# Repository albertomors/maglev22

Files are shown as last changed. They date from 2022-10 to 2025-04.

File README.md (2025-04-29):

# Re-design of a magnetic levitation platform: from an early prototype to a working system
Bachelor Thesis in Electronic Engineering - November 2022 - Università degli Studi di Padova @unipd

## Abstract
This work documents the modelling and re-designing of a maglev platform intended to become a take-home lab for students interested in control engineering. The platform, initially designed by a team of Norwegian students, presented a series of inefficiencies and limitations that this work seeks to remove. Thus, the final goal of this project is to fully develop and test an improved maglev platform.

The thesis introduces both the theoretical framework behind the modeling of the system, and the specific frameworks for designing and analysing the various electronic subsystems that were deemed to be improvable. In doing so, this work discusses those subsystems, lists a set of potential solutions together with their pros and cons, and selects potential choices one may take, given the techno-economic constraints surrounding the project. In addition, practical implementation issues are discussed, giving in this way an overview of which parts of the systems should be further analyzed and fine tuned before arriving at a system that is ready for production. 

The most challenging part of this project has been entering into it without clear guidelines of the design choices made by the previous team. It is precisely for this reason that this work does not just aim at reporting on the project itself, but also at offering documentation that is as clear as possible, intended to help a potential future team bringing the project to its next phase.

[Click here to read the dissertation](https://github.com/albertomors/maglev22/blob/b5a09330e3dea7a6b91397591241a9633b680332/Bachelor%20Thesis%20-%20maglev22.pdf)

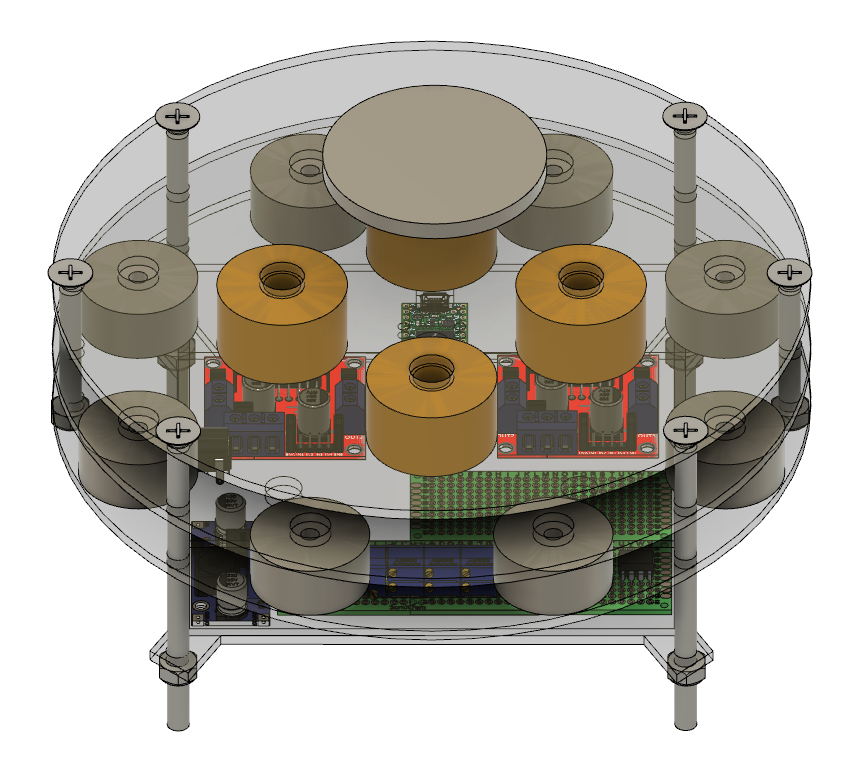
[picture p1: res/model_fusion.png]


## Structure

```
maglev22/
├── code                               # C++/arduino code for the Teensy4.0 microcontroller
├── datasheets                         # details about the electronic components used in the project  
├── matlab                             # modelling scripts   
├── schematics                         # kicad, fritzing and multisim schematics
├── Bachelor Thesis - maglev22.pdf     # Dissertation
├── LICENSE                            # License information
├── README.md                          # Project documentation
└── model_fusion.png                   # Picture of the prototype built
```

## What's next
In the meantime the project has moved on, see https://github.com/Hansolini/Take-home-Maglev-lab for the main repo handling this project. I contributed again to it with the design of the PCB for it's version 2.6 and 3.0. Below some videos and pictures of them.

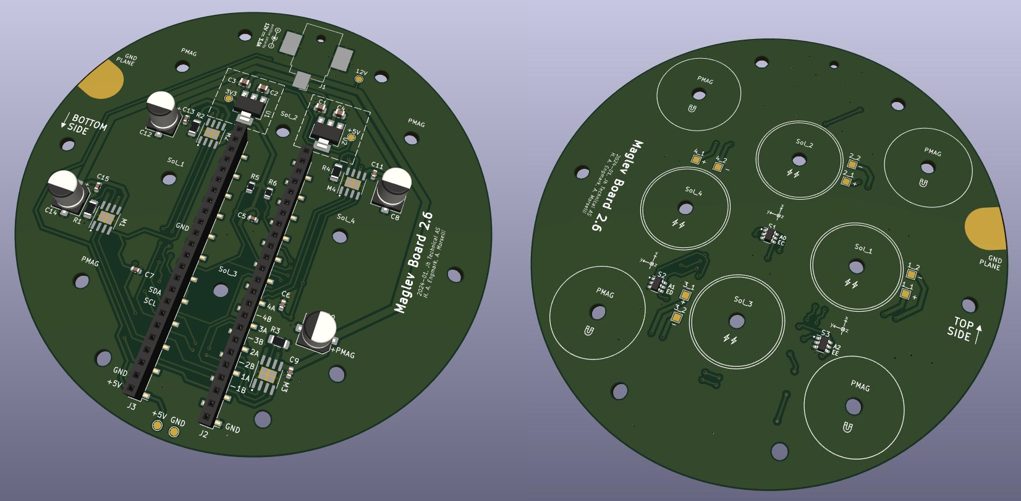
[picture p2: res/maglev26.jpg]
 \
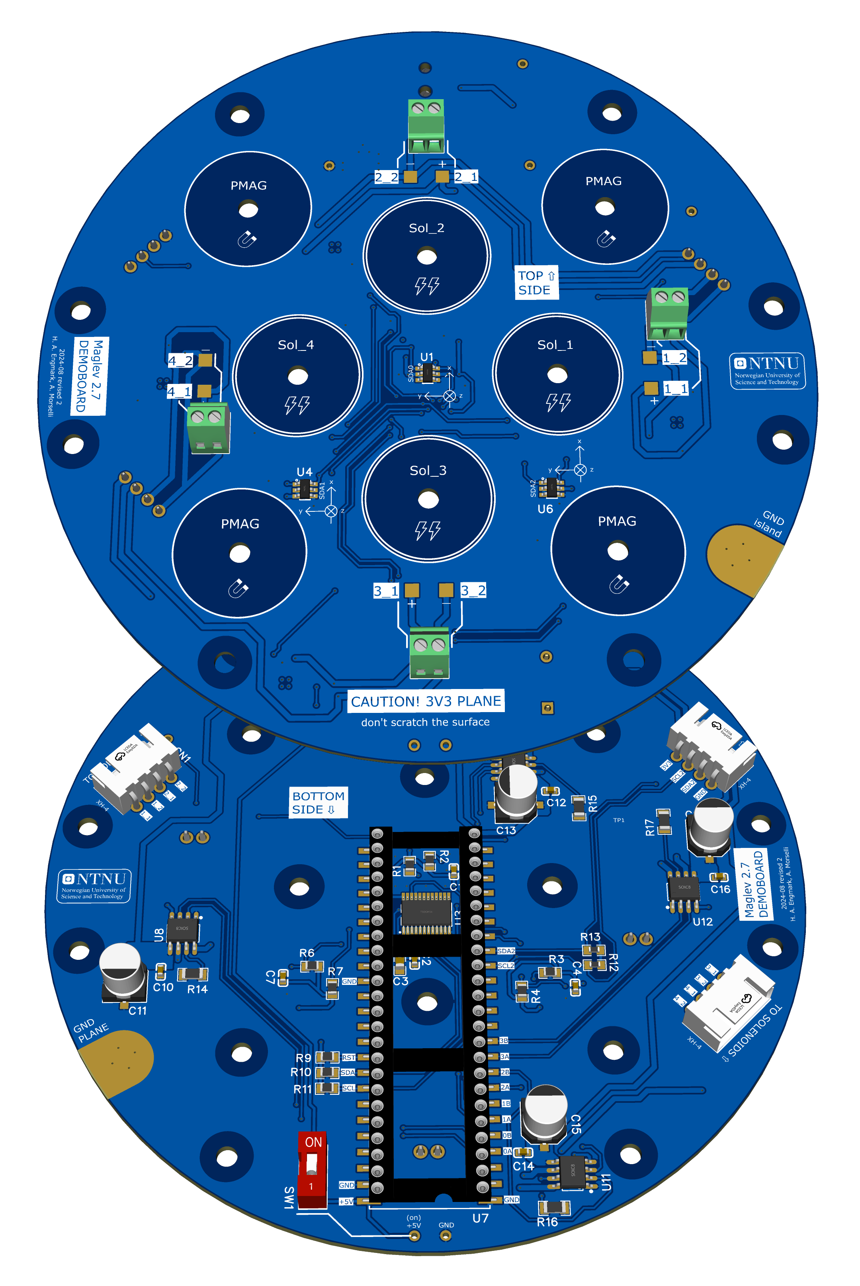
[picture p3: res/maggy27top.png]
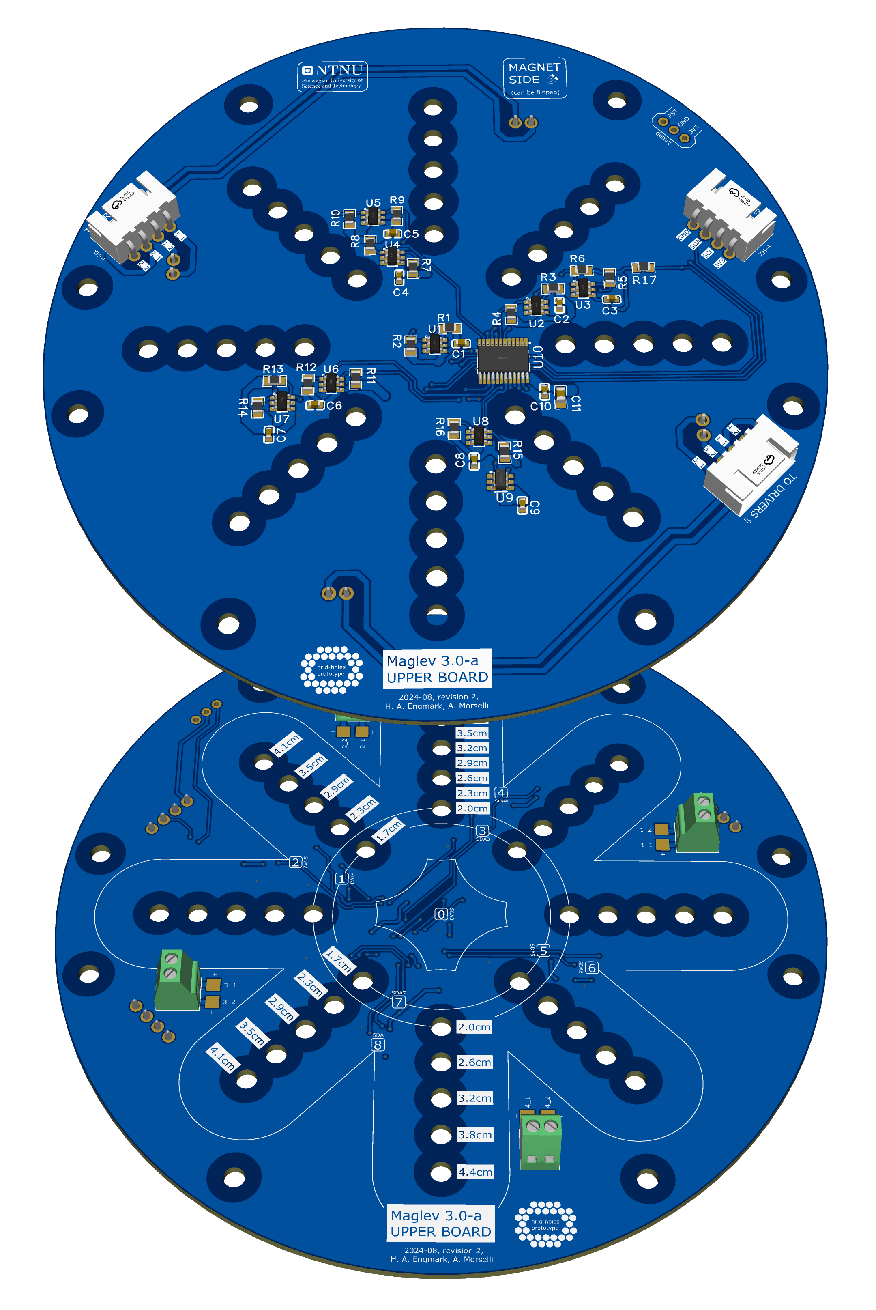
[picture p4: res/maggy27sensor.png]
  \
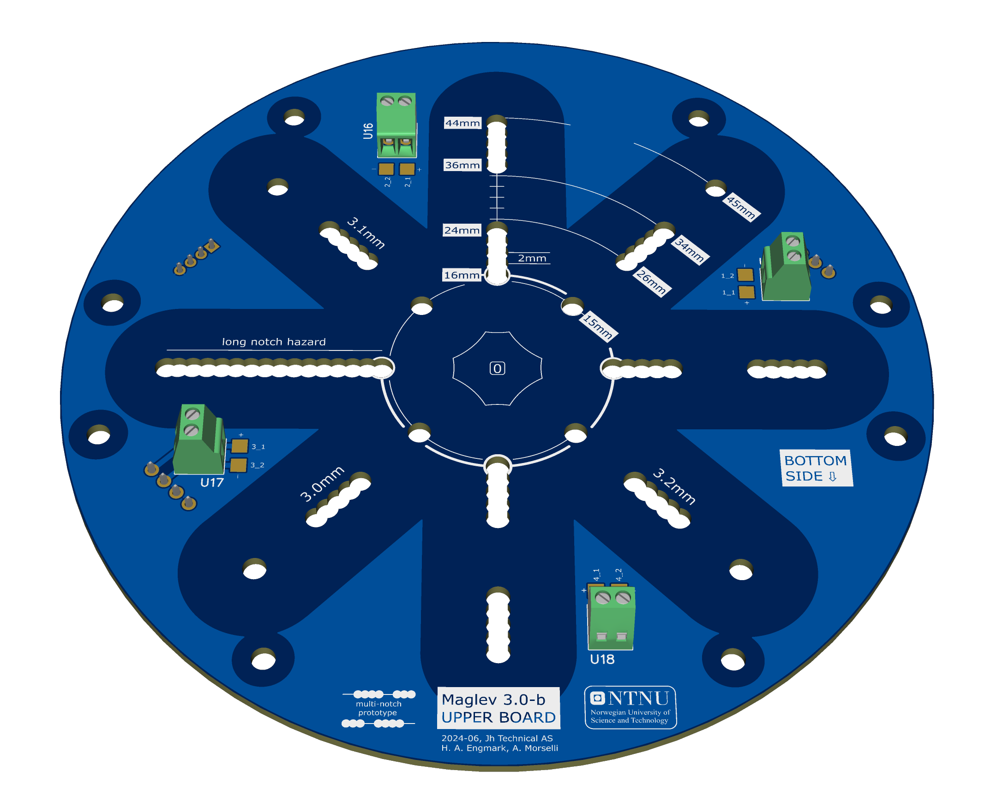
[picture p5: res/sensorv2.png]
 

## License
This project is licensed under the MIT License. See the [LICENSE](LICENSE) file for more details.

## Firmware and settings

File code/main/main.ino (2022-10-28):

/*
 * Author: Morselli Alberto
 * Project: maglev22
 * Date: Summer-Autumn 2022
 *
 *
 * -SENSOR_x1 face X1-coil and gives his back to X2-coil
 *         x2 face X2-coil               back to X1-coil
 * -SENSOR_y1 face Y1-coil and gives his back to Y2-coil
 *         y2 face Y2-coil               back to Y1-coil
 * -SENSOR_z face the top
 * 
 * Ff a magnet SOUTH pole approaches the sensor (inflow in the magnet) the sensor drive the v_outage higher.
 * This 5-sensor configuration leads to positive deviation on x1 and y1 sensors when the magnet moves towards X1 and Y1 coils,
 * and negative when he moves away. x2 and y2 sensors have the opposite behaviour. z sensor leads to positive devs when the magnet
 * goes down and positive when it goes up.
 *
 * With the connection made on the board OUT1-2-3-4 are connected respectively to X1A-B-Y1A-B. Same pattern for motor driver 2.
 * Wires A and B are connected respectively to EXTernal and INTernal heads of the wire's coil.
 * Setting A-B to HIGH-LOW leads to SOUTH pole on his top and NORTH pole on his bottom, R-epelling the levmag that has SOUTH pole on his bottom.
 *         A-B to LOW-HIGH          NORTH pole on his top and SOUTH pole on his bottom, A-ttracting
 *
 * MOTOR-DRIVER 1 pilots X1- and Y1-coils
 * MOTOR-DRIVER 2 pilots X2- and Y2-coils
 *
 * TEENSY4.0 pins from 2 to 7 are dedicated to MOTOR DRIVER 1 / SX and controls X1/Y1 coils
 *                from 8 to 12+14 are dedicated to MOTOR DRIVER 2 / DX and controls X2/Y2 coils
 *                from 15 to 19 are dedicated to the SENSORS X,Y,Z (based on 3 or 5 sensor implementation)
 *                20 is dedicated to read Vref supplied by INA128
 *
 * there are two strategies to set coils behaviour:
 *    the OLD: set the coils ALWAYS in a dual behaviour (one R and the other A) prioritizing ux/uy value and adding after uz.
 *            when uz is high and ux/uy is low this can leads to saturate one of the two pwm vals to 0
 *
 *            example: ux=5, uz=50 => set X1-R with +5+50 = +55 => (R with pwm = 55)
 *                                        X2-A with +5-50 = -45 clamped to 0 because of saturation => (A with pwm = 0)
 *
 *    the NEW: calcs before ux+uz for X1 and -ux+uz for X2 (dual action for x/y-axis but same for z-axis) and regardings to >=0 or <0 sets
 *            the coils. This means that in some cases both coils can A-ttract or R-epel.
 *
 *            example: ux=5, uz=50 => x1_val = 5+50 = 55 (R with pwm = 55)
 *                                    x2_val = -5+50 = +45 (R with pwm = 45)
 */

#include <SimpleKalmanFilter.h>
#include "defines.h"

void setup()
{
  analogReadResolution(10);
  analogReadAveraging(3);
  analogWriteResolution(8);

  //Code running freq is approx 10 kHz
  analogWriteFrequency(ENABLE_X1, 32000);
  analogWriteFrequency(ENABLE_X2, 32000);
  analogWriteFrequency(ENABLE_Y1, 32000);
  analogWriteFrequency(ENABLE_Y2, 32000);
  
  // set pins
  for(int i=2; i<=12; i++){ pinMode(i,OUTPUT); }
  pinMode(14,OUTPUT);
  for(int i=15; i<=20; i++){ pinMode(i,INPUT); }
  
  // start with coils "off"
  digitalWrite(X1_A, LOW);
  digitalWrite(X1_B, LOW);
  digitalWrite(X2_A, LOW);
  digitalWrite(X2_B, LOW);
  
  digitalWrite(Y1_A, LOW);
  digitalWrite(Y1_B, LOW);
  digitalWrite(Y2_B, LOW);
  digitalWrite(Y2_A, LOW);
}

// --------------------------------------------------------------

double ex[3] = {0.0,0.0,0.0}; // e_k, e_(k-1), e_(k-2)
double ey[3] = {0.0,0.0,0.0};
double ez[3] = {0.0,0.0,0.0};

double ux[2] = {0.0,0.0}; // u_k, u_(k-1)
double uy[2] = {0.0,0.0};
double uz[2] = {0.0,0.0};

uint16_t readings[5];
double v_out[5], dv_out[5], dv_in[5], filt[5], u[3], g[3];

double dwx2,dwy1,wx1,wx2,wy1,wy2;

// to estimate e[i], aka measurement uncertainty, read and and use n>> values printed on the serial monitor 
// to calc std deviation [corrected, the one with n-1] = s
// then to get the 99.7% coverage interval multiply s by 3 to get 3*s
double e[6] = {.005,.005,.005,.005,.005,.002};
SimpleKalmanFilter kf[6] = {SimpleKalmanFilter(e[0],e[0],0.01), \
                            SimpleKalmanFilter(e[1],e[1],0.01), \
                            SimpleKalmanFilter(e[2],e[2],0.01), \
                            SimpleKalmanFilter(e[3],e[3],0.01), \
                            SimpleKalmanFilter(e[4],e[4],0.01), \
                                                                \
                            SimpleKalmanFilter(e[5],e[5],0.01)}; //last one is for vref
unsigned long t1,t2,t3;
double fs = 0;

// --------------------------------------------------------

void loop()
{
  t1 = micros();
  
  for(int i=0; i<5; i++){
    readings[i] = analogRead(SENSOR_ARRAY[i]);

    v_out[i] = readings[i]*n2v; //map from [0 : 1024] to [0 : 3.3V] ...
    dv_out[i] = v_out[i] - vref; // ... and subtract Vref to have a [-vref : vref] value
    dv_in[i] = dv_out[i]*o2i; //divide by G
    
    filt[i] = kf[i].updateEstimate(dv_in[i]); //filter datas

//    Serial.print(filt[i],4);
//    Serial.print(" ");
  }

  t2 = micros()-t1;

  /* This is the couples of COILS and sensors placement. If the maglev is so much off-center                  
   * towards X1 the right sensor to priotize is y1 instead of y2, more sensible. Same thing
   * if the maglev is towards Y2 the most sensitive and accurate sensor is x1 instead of x2.
   * If it's almost on the center the weights don't differ too much.
   *                   
   *                     x-axis
   *                       ^
   *                       |
   *     
   *                     X1-y1
   * 
   * y-axis  <-- Y1-x2     o     Y2-x1
   * 
   *                     X2-y2
   *                     
   *                     
   */

  dwx2 = (filt[2] - filt[3]) * 0.5 / 0.4; // use y to estimate the X-weights [how much priority give to x2 than to x1]
  wx2 = 0.5 + dwx2 * 0.5;
  wx1 = 1 - wx2;
  
  dwy1 = (filt[0] - filt[1]) * 0.5 / 0.4; // instead use x to estimate the Y-weights [how much priority give to y1 than to y2]
  wy1 = 0.5 + dwy1 * 0.5;
  wy2 = 1 - wy1;

//  Serial.print("#W> ");
//  Serial.print(wx1);
//  Serial.print(" ");
//  Serial.print(wx2);
//  Serial.print(" ");
//  Serial.print(wy1);
//  Serial.print(" ");
//  Serial.println(wy2);

  // here you can override values to test the difference
//  wx1 = 0.5; wx2 = 0.5; wy1 = 0.5; wy2 = 0.5;

  // compute x,y,z values with the chosen positive direction towards x1,y1,bottom
  // SO: positive ux/uy contributes says the levmag is towards x1,y1 or flipped on x1,y1.
  //     [if is towards x1 but flipped on x2 the total ux may be <=>0 !!! #TODO]
  //     uz >= 0 says the levmag is lower than z_eq, towards the bottom
   
  u[0] = filt[0]*wx1 - filt[1]*wx2;
  u[1] = filt[2]*wy1 - filt[3]*wy2;
  u[2] = filt[4];

//  Serial.print("#g> ");
  // get gauss value
  for(int i=0; i<3; i++){
    g[i] = u[i] * sens_1;
//    Serial.print(g[i]);
//    Serial.print(" ");
  }

  //correct signs of the errors
  ex[0] = g[0]; //towards x1 => positive val => x1 repel (>=0)
  ey[0] = g[1]; //towards y1 => positive val => y1 repel (>=0)
  ez[0] = -g[2]; //towards z => positive val => to lift all coils must attract (<0) => sign change

//  Serial.print("#e> ");
  Serial.print("ex:");
  Serial.print(ex[0]);
  Serial.print(" ");
  Serial.print("ey:");
  Serial.print(ey[0]);
  Serial.print(" ");
  Serial.print("ez:");
  Serial.print(ez[0]);
  Serial.print(" ");

  // compute controller gain - Velocity form
  ux[0] = ux[1] + KP_X*(ex[0]-ex[1]) + KI_X*ex[0] + KD_X*(ex[0] - 2*ex[1] + ex[2]);
  uy[0] = uy[1] + KP_Y*(ey[0]-ey[1]) + KI_Y*ey[0] + KD_Y*(ey[0] - 2*ey[1] + ey[2]);
  uz[0] = uz[1] + KP_Z*(ez[0]-ez[1]) + KI_Z*ez[0] + KD_Z*(ez[0] - 2*ez[1] + ez[2]);

//  Serial.print("#pid> ");
  Serial.print("ux:");
  Serial.print(ux[0]);
  Serial.print(" ");
  Serial.print("uy:");
  Serial.print(uy[0]);
  Serial.print(" ");
  Serial.print("uz:");
  Serial.print(uz[0]);
  Serial.print(" ");
  
  // update values
  ex[2] = ex[1]; ex[1] = ex[0];
  ey[2] = ey[1]; ey[1] = ey[0];
  ez[2] = ez[1]; ez[1] = ez[0];

  ux[1] = ux[0];
  uy[1] = uy[0];
  uz[1] = uz[0];

  // give priorities to the controller along the axis [contrain between [-255<=-LIM:+LIM<=255]
  ux[0] = round(constrain(ux[0],-MAX_OUTPUT_X,+MAX_OUTPUT_X));
  uy[0] = round(constrain(uy[0],-MAX_OUTPUT_Y,+MAX_OUTPUT_Y));
  uz[0] = round(constrain(uz[0],-MAX_OUTPUT_Z,+MAX_OUTPUT_Z)); //reduced

  turn_X_NEW_final(ux[0], uz[0]);
  turn_Y_NEW_final(uy[0], uz[0]);

  Serial.println();
//  Serial.print(fs);
//  Serial.print(" Hz # ");

  t3 = micros() - t1;
  fs = 1000000.0/t3;
}

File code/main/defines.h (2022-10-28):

/*
 * Author: Morselli Alberto
 * Project: maglev22
 * Date: Summer-Autumn 2022
 * 
 * 
 * This file contains the settings used for the implementation:
 *   -TEENSY4.0 pin connections [editable here]
 *   -Code constants
 *   -PID parameters
 *
 * TEENSY4.0 pins from 2 to 7 are dedicated to MOTOR DRIVER 1 / SX and controls X1/Y1 coils
 *                from 8 to 12+14 are dedicated to MOTOR DRIVER 2 / DX and controls X2/Y2 coils
 *                from 15 to 19 are dedicated to the SENSORS X,Y,Z (based on 3 or 5 sensor implementation)
 *                20 is dedicated to read Vref supplied by INA128
 */

// pin connections ---------------------------------------------------------------

// motor driver 1 - SX - controls X1-coil and Y1-coil
#define X1_A 3
#define X1_B 4
#define Y1_A 5
#define Y1_B 6

#define ENABLE_X1 2
#define ENABLE_Y1 7

// motor driver 2 - DX - controls X2-coil and Y2-coil
#define X2_A 9
#define X2_B 10
#define Y2_A 11
#define Y2_B 12

#define ENABLE_X2 8
#define ENABLE_Y2 14

// hall effect sensors
#define SENSOR_x1 15
#define SENSOR_x2 16
#define SENSOR_y1 17
#define SENSOR_y2 18
#define SENSOR_z 19
const uint8_t SENSOR_ARRAY[5] = {SENSOR_x1, SENSOR_x2, SENSOR_y1, SENSOR_y2, SENSOR_z};

#define VREF_PIN 20

// others sensors constants ------------------------------------------------------------

const double n2v = 3.3/1024;
const double v2n = 1.0/n2v;
const double i2o = 3.52; // ad623 gain set TODO
const double o2i = 1.0/i2o;
const double vref = 1.584;

const double sens = 2; // the value is in [mV/gauss], sens1;
const double sens_1 = 1000.0/sens; // now the value is in [gauss/V]  

// output limitations if set ------------------------------------------------------------

const int MAX_OUTPUT_X = 255;
const int MAX_OUTPUT_Y = 255;
const int MAX_OUTPUT_Z = 100; // prioritize x & y control

// pid parameters -----------------------------------------------------------------------

#define KP_X 1.2
#define KD_X 0.3
#define KI_X 0

#define KP_Y KP_X
#define KD_Y KD_X
#define KI_Y 0

#define KP_Z 0.8
#define KD_Z 0.1
#define KI_Z 0
